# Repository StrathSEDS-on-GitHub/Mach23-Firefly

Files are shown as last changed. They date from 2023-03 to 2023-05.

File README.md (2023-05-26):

# Firefly
Archival repository for the Firefly Project. Casually referred to as Universal Mainboard within StrathSEDS. It is the spirit successor of SHAMANBoard.

Firefly is modular flight computer aimed at model rockets. Its most important features are:
 - STM32F412 MCU
 - GNSS navigation
 - 2 double protected pyro channels
 - 9DoF IMU
 - BMP581 based pressure altimeter
 - UART, SPI, I2C and GPIO expansion headers
 - NeoPixel compatible RGB LEDs
 - W25Q flash and SDCard support for logging
 - LLCC68 based LoRa radio
 - USB-C 😎
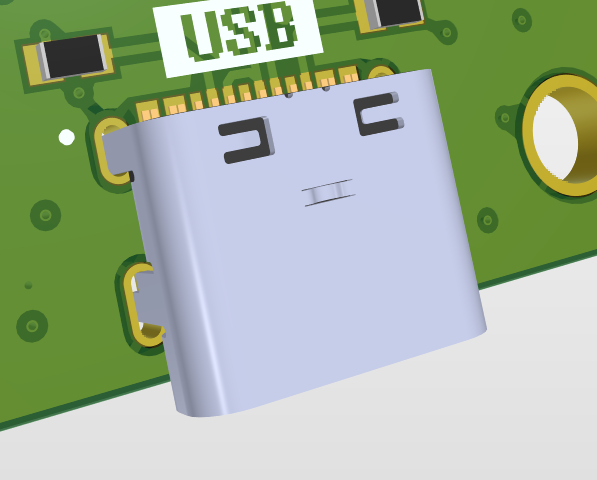
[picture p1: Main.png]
render of the PCB


You can use the Outjob files for generating manufacturing files, all of which are included in the JLCPCB folder

# Known Issues
 - QSPI IO2 connected to PE3 not PE2
 - IMU BOOT pin tied low instead of high
 - Payload board I2C pins swapped
 - Umbilical regulator capacitor reversed
 - Umbilical regulator enable pin should be tied to input not output
 - Potential unnecessary use of I2C buses resulting in lack of SWO
 - lack of reverse current protection diode between USB and Vbat
 - lack of hole in the PCB for the GPS antenna
 
# V2 new feature ideas
 - reposition LEDs for better usage of space
 - RPP MOSFET on battery input

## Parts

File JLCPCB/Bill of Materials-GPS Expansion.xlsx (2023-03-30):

Comment | Value | Designator | Footprint | LCSC Part #
S8411-45R |  | BT1 | FP-S8411-45R-MFG
Generic-Capacitor | 4.7uF | C1 | FP-0603-L_1_6_0_15-W_0_81-IPC_C | C19666
Generic-Capacitor | 100nF | C2, C4 | FP-0603-L_1_6_0_15-W_0_81-IPC_C | C14663
Generic-Capacitor | 10uF | C3 | FP-0603-L_1_6_0_15-W_0_81-IPC_C | C96446
Male header 1x5 2.54mm |  | P1 | 61300511121
L80-M39 |  | U1 | QUEC-L80-M39-12_V
WS2812B |  | U2, U3 | ADAI-WS2812B_V | C4154882

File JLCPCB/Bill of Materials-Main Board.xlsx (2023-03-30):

LCSC PART # | Description | Designator | Footprint | Value
C1002 | 0603 600Ω ±25% DCR=0.45Ω 0.2A | FB1, FB2 | FP-BLM18-0_15-0_1-t0_6-IPC_B | 600R
C2930107 | Generic 0603 Resistor | R2 | RESC1609X50X30ML8T20 | 487k
C22966 | Generic 0603 Resistor | R27_P1, R27_P2, R36 | RESC1609X50X30ML8T20 | 270R
C14858 | Generic 0603 Capacitor | C30 | FP-0603-L_1_6_0_15-W_0_81-IPC_C | 100pF
C14663 | Generic 0603 Capacitor | C2, C3, C4, C5, C6, C7, C8, C9, C13, C19, C20, C21, C22, C23, C24, C27, C28, C29 | FP-0603-L_1_6_0_15-W_0_81-IPC_C | 100nF
C25803 | Generic 0603 Resistor | R37 | RESC1609X50X30ML8T20 | 100k
C23172 | Generic 0603 Resistor | R26_P1, R26_P2 | RESC1609X50X30ML8T20 | 43k
C21122 | Generic 0603 Capacitor | C25_P1, C25_P2, C26_P1, C26_P2 | FP-0603-L_1_6_0_15-W_0_81-IPC_C | 22nF
C22859 | Generic 0603 Resistor | R4, R5 | RESC1609X50X30ML8T20 | 10R
C25804 | ±1% 1/10W Thick Film Resistors 75V ±100ppm/℃ -55℃~+155℃ 10kΩ 0603 Chip Resistor - Surface Mount ROHS | R15, R17, R18 | RESC1608X55X25ML10T15 | 10k
C25804 | Generic 0603 Resistor | R1, R3, R6, R13, R16, R21, R22, R23, R24, R25, R28_P1, R28_P2, R29_P1, R29_P2, R30, R31, R35, R38 | RESC1609X50X30ML8T20 | 10k
C156247 | Crystal 16MHz ±20ppm (Tol) ±30ppm (Stability) 8pF FUND 80Ohm Automotive 4-Pin SMD | Y1 | FP-NX3225GA-MFG | 8pF
C280830 | Crystal 32.7680KHZ 7PF SMD | Y2 | FP-NX3215SA-MFG | 7pF
C37474 | CAP CER 6PF 50V C0G/NP0 0603 | C16, C17 | FP-CL10-IPC_B | 6pF
C23186 | Generic 0603 Resistor | R19, R20 | RESC1609X50X30ML8T20 | 5.1k
C53987 | Generic 0603 Capacitor | C18 | FP-0603-L_1_6_0_15-W_0_81-IPC_C | 4.7uF
C59526 | 50V 4.3pF C0G ±0.25pF 0603 Multilayer Ceramic Capacitors MLCC - SMD/SMT ROHS | C14, C15 | FP-CL10-IPC_B | 4.3pF
C1604 | Generic 0603 Capacitor | C11, C12 | FP-0603-L_1_6_0_15-W_0_81-IPC_C | 2.2nF
C4190 | Generic 0603 Resistor | R7, R8, R9, R10, R11, R12, R39, R40 | RESC1609X50X30ML8T20 | 2.2k
C15849 | Generic 0603 Capacitor | C10, C32 | FP-0603-L_1_6_0_15-W_0_81-IPC_C | 1uF
C21190 | Generic 0603 Resistor | R32, R33, R34 | RESC1609X50X30ML8T20 | 1k
C146362 | Single 2-input AND gate | U6 | SOT65P210X110-5N
C965555 | Intelligent control LED light source, SMD-4 | U11, U12 | LED_WS2812-2020
 | 1.27mm (0.05in.) pitch, Shrouded header, 10 contacts | J8 | 2002151100010T4LF
 | Female Header, Pitch 2.54 mm, 1 x 8 Position, Height 8.5 mm, Tail Length 3.2 mm, -40 to 105 degC, RoHS, Bulk | J2, J3 | SLIN-PPPC081LFBN-RC_V
 | Headers & Wire Housings Tiger Buy Socket Strip with Square Tails, 0.100 Pitch | J1 | SMTC-SSQ-105-02-X-S-RA
 | IMU Accel/gyro/mag I2C 32 Bit | U7 | FP-BNO085-MFG
 | Kingstate 5V dc PCB Mount Electromagnetic Buzzer | LS1 | KXG1203C
 | LoRa-CC68 targeting 868MHz and with a TXCO | U2 | LoRa-CC68-868-TCXO-Footprint-1
 | Pressure Sensor 4.35PSI ~ 18.13PSI (30kPa ~ 125kPa) Absolute 10-WFLGA | U8 | BMP581
 | Printed circuit board terminals, 3.50 mm, Number of poles: 6, 90, Solder pin length: 3.5 mm, black, PUSH IN with actuator, Clamping range, max. [rated connection]: 1.5 mm, Tube | J4, J6 | SHDR12W80P700X350_2X6_2170X1400X850P
 | RF Connectors / Coaxial Connectors SMA RA PCB Mount, Jack, Gold, 50 , Through Hole Pin | J7 | PCBSMAFRAHT
 | Polymeric PTC Resettable Fuse 30V 0.75A Surface Mount 1206 | F1_P1, F1_P2 | RESC3115X65N
C7989 | 5V and Adjustable Micropower LDOs | B1 | SOIC127P600X175-8N
C8598 | Schottky Barrier Rectifier, 40 V, 1 A, -65 to 125 degC, 2-Pin SOD123, RoHS, Tape and Reel | D3 | MCC-SOD123_V
C8667 | PMBT3904 - NPN switching transistor | Q5 | SOT95P230X110-3N
C20917 | N沟道 VDS=30V VGS=±12V ID=5.7A P=1.4W | Q1 | FP-SOT23-IPC_C
C22962 | Res Thick Film 0603 220 Ohm 1% 1/10W ±100ppm/°C Molded SMD SMD Paper T/R | R14 | FP-CRCW0603-e3-IPC_C
C23791 | IC REG LDO 3.3V 0.5A 8SOIC | U3 | D0008A_L
C64898 | DIODE GEN PURP 1KV 1A SOD123FL | D1, D4 | MCC-SOD-123FL_V
C97521 | FLASH - NOR Memory IC 128Mb (16M x 8) SPI - Quad I/O, QPI, DTR 133 MHz 8-SOIC | U4 | SOIC127P790X216-8N
C146318 | MOSFET Small Signal MOSFET V=30V | Q4 | SSM6J507NULF
C221880 | Switch Tactile N.O. SPST Round Button Gull Wing 0.05A 12VDC 100000Cycles 1.57N SMD T/R | SW1, SW2 | CKCP-PTS645S_V
C293569 | Conn Micro SD Card HDR 8 POS 1.1mm Solder RA SMD Embossed T/R 0.5A/Contact | SD1 | MOLX-473521001_V
C315567 | MOSFET N Trench 30V 30A(Tc) 2.2V @ 250uA 5 m @ 20A,10V DFN-8_3x3 EP RoHS | Q3_P1, Q3_P2 | AON7544
C400102 | AVX Electrolytic Capacitor 22uF 10V dc Electrolytic Solid +/-10% Tolerance TPS Series | C1, C31 | CAPPM3528X210N
C434419 | SZYY0603R | D2_P1, D2_P2, D5 | FP-LTST-C190GKT-MFG
C727951 | STMICROELECTRONICS - STM32F412VGT6 - ARM MCU, STM32 Family STM32F4 Series Microcontrollers, ARM Cortex-M4F, 32bit, 100 MHz, 1 MB, 256 KB | U1 | QFP50P1600X1600X160-100N
C2683769 | High Speed, Low-Side, Single Gate Driver | U5_P1, U5_P2 | SOT95P245X110-5N
C2757930 | PTC Resettable Fuse: 2A Hold, 4A Trip, 0603 | RT2 | THRMC1608X95N
C2927300 | YTC-TC16S-23 USB Type C Surface Mount PCB Socket 3A | J5 | VALCON_CSP-USC16-TR

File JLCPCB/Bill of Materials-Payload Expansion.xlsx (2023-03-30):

Comment | Value | Designator | Footprint | LCSC Part #
Generic-Capacitor | 100nF | C1 | FP-0603-L_1_6_0_15-W_0_81-IPC_C | C14663
SM4007PL-TP |  | D1 | MCC-SOD-123FL_V | C64898
1824480000 |  | E1 | LSF_SMT_3_5_90_08
5-146278-8 |  | J1, J2 | HDRV8W56P0X254_1X8_1991X234X872P
Generic Resistor | 400mR | R1 | RESC2512(6432)_N
Generic-Resistor | 6M | R2, R4 | RESC1609X50X30ML8T20 | C322196
Generic-Resistor | 2M2 | R3 | RESC1609X50X30ML8T20 | C322103
INA219AIDR |  | U1 | D0008A_L | C138706

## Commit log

2023-03-30 Purchase Snapshot
    We did it! We did it! We did it! Yeah!
    [Board Overview.SchDoc, Connectors.SchDoc, GPS Expansion.PrjPcb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]
2023-03-30 Adding interconnect board
    forgor
    [Interconnect.PcbDoc, Interconnect.SchDoc, Umbilical and battery interconnect.PrjPcb]
2023-03-30 initial README, add manuf files
    [Bill of Materials-GPS Expansion.xlsx, Bill of Materials-Main Board.xlsx, Bill of Materials-Payload Expansion.xlsx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]
2023-05-26 Correction on IO2 pin mixup
